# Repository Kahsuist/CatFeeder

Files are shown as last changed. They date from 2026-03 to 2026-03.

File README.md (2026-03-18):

# Автокормушка для кота. ESP-32, WiFi, Bluetooth, расписание.






 - Автоматическая кормушка для домашнего питомца. Не нужно следить за миской кота и контролировать его норму, чтобы он не превратился в колобка, как некоторые домашние питомцы. Экономит время и устраняет одну заботу - помнить о кошачьей миске.

## Возможности

- Не очевидная функция - возможность дрессироваки кота.
- Расписание гибко задается со смартфона через bluetooth.
- Имеет внутренние часы с синхронизацией в интернет, благодаря чему по расписанию выдает корм по норме.
- Имеется педаль экстренной подачи, которую может нажать и сам кот, если научится.
- Так же экстренно можно насыпать корм со смартфона.
- Расписание сохраняется в постоянной памяти и не теряется после отключения питания.
- Емкость контейнера 3 литра в текущем исполнении.
- Имеется защита от застревания корма с попытками протолкнуть.

## Фото устройства

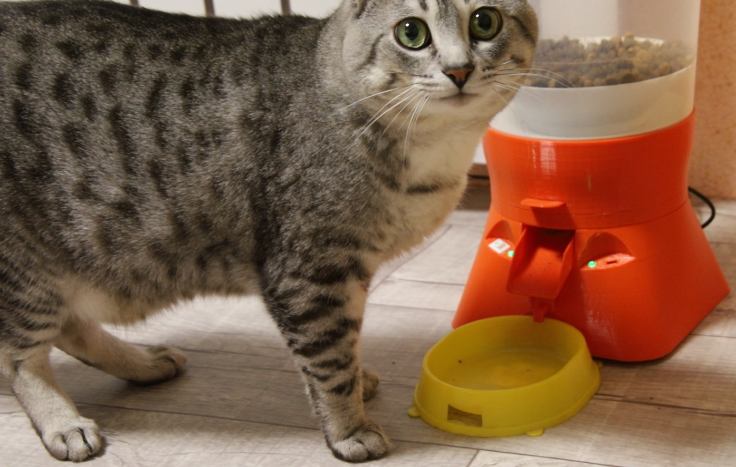
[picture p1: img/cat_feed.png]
Собранное устройство сверху
  
*Собранное устройство. И кот!*

## Электрическая схема

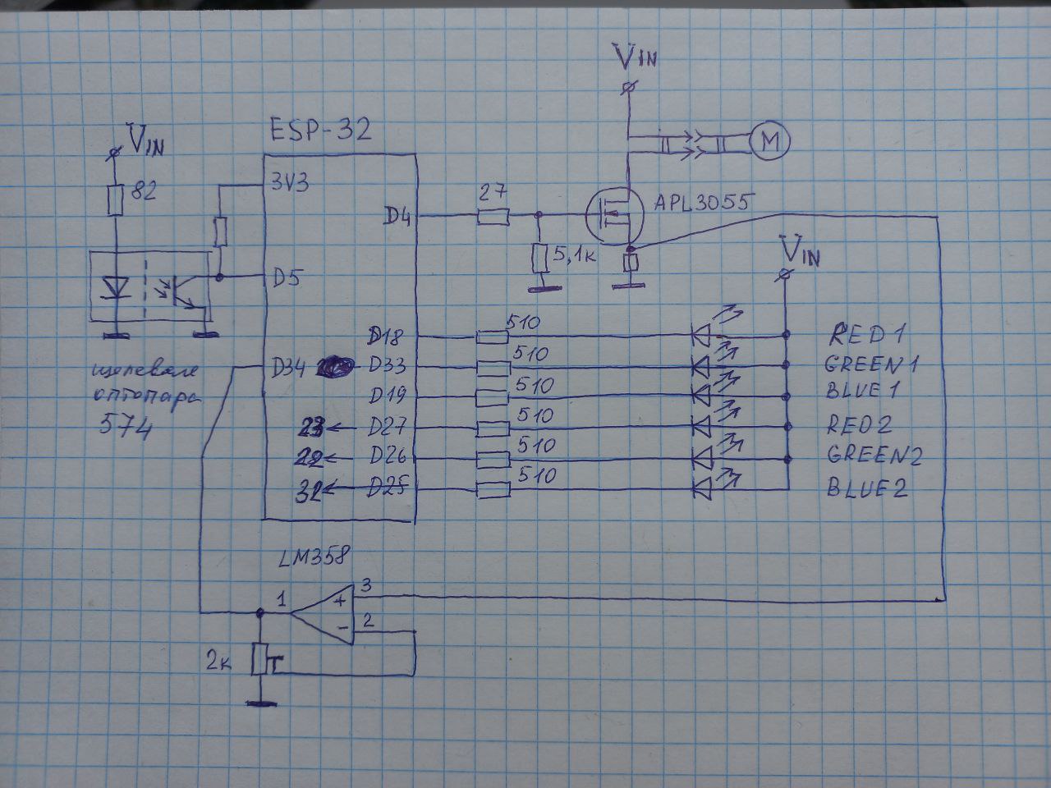
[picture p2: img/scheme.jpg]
Схема на бумаге
  
*Полная электрическая схема*

Подробные файлы схемы:  
- (в планах) ~~[KiCad проект → schematic.kicad_sch](hardware/schematics/)~~
- (в планах) ~~[Экспорт в PDF → schematic.pdf](hardware/schematics/schematic.pdf)~~

## Как открыть и собрать проект

1. Для прошивки микроконтроллера используется Arduino, файл kormushka.ino (файл копируй вместе с папкой, т.к. ардуино требует одноименных названий того и другого). Перед прошивкой внеси данные своей WiFi-сети.
2. Детали кормушки напечатаны на 3д принтере, STL-модели находятся в папке 3Dmodels. ВАЖНО!!! Поскольку это был первый экземпляр, то без мелких ошибок не обошлось, по этому имеются проставки и удлинители. В будущем если проект вызовет интерес, планирую переработать модели, чтобы сборка происходила без лишних телодвижений. В данной версии потребуется не только склейка но и подрезка. Часть деталей изначально задумана из двух половинок, так как напечатать их на принтере целиком крайне не выгодно по филаменту. Проще склеить. Я печатал PETG, он не воняет и легко склеивается дихлорметаном.
3. Радиоэлектроныне компоненты: ESP32, двигатель с редуктором с алиэкспресс JGA25-370 с 16-25 об/мин. 6-12 вольт. Важно, чтобы двигатель давал достаточный момент при напряжении в 5 вольт. Я использовал двигатель с редуктором привода колес от робота-пылесоса на 12 вольт - он такой же, как на али.
4. Полевой ключ APL3055 - любой подобный выдержит ток до 1-2 ампер.
5. Щелевая оптопара тоже дешевая и широкоприменяемая. Я использовал из того-же робота-пылесоса, на ней обозначение 574. Но встречал такие же в принтерах, ксероксах, сканерах и прочих приборах с конечными датчиками-оптопарами.
6. Операционник LM358 так же очень широко распространен.
7. Светодиоды RGB в одном корпусе с общим анодом. На алиэкспресс 50 штук за 120 руб.
8. Резисторы любые. Я паял как прототип на макетке, мне были удобны smd.

## Как использовать

1. Насыпал корм, включил в розетку. Устройство само подключится к WiFi и синхронизирует часы по интернет.
2. В смартфоне открываешь bluetooth-устройства, находишь CatFeeder, подключаешся.
3. Запускаешь любой bluetooth-терминал, коннектишся к выбранному catfeeder-y
4. Список команд<br>
    **SET 7:15 2** - установить, время в часах:минутах, количество доз. Одна доза = один сектор поворота (из шести). 2 - соответственно два сектора. В моем случае 1 доза это 15 грамм корма. Если поставить 2 то насыплется 30 грамм и так далее.<br>
    **DEL 7:15** - удалить конкретную запись, если она есть.<br>
    **LIST** - показать всё расписание<br>
    **CLEAR** - удалить всё расписание<br>
    **SAVE** - сохранить расписание в память. ВАЖНО!!! Если не сохранить расписание, то оно пропадет после выключения питания.<br>
    **RUN** - насыпать одну дозу корма (15гр.)<br>

## Зависимости / Требования

Для прошивки под линукс открываем терминал, вводим команду *sudo chmod a+rw /dev/ttyACM0* либо *sudo chmod a+rw /dev/ttyUSB0*, чтобы система получила доступ к устройству, то есть задать права доступа. Теперь можно прошивать из ардуино. Как это делается в Windows - расскажите, добавлю сюда. Предполагаю, что понадобится установка драйверов и другие танцы с бубном.

## Disclaimer

Это первая версия readme, в ней обязательно должны быть ошибки и недочеты, по этому обращайтесь по контактам ниже, с вашей помощью устраним баги для будущих посетителей. 

Это рабочий отлаженный прототип. Но пердполагается апгрейд проекта (аккумуляторы, приложение на смартфон, печатная плата с герберами под производство и др.)
Используй на свой страх и риск.  

Сообщения об ошибках / PR приветствуются!

## Лицензия

MIT License — см. файл [LICENSE](LICENSE)

## Контакты

Если хотите со мной связаться: телега *@kahsuist*

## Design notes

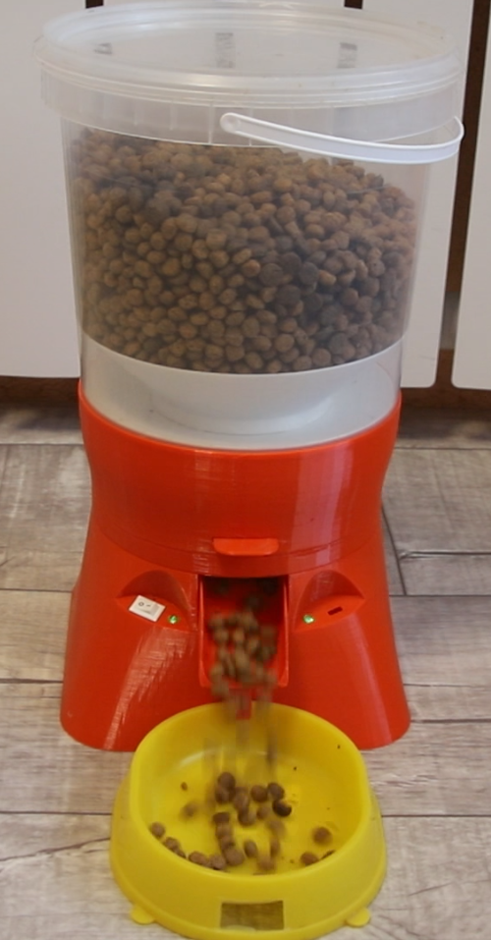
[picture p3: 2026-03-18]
img/catfeeder.png

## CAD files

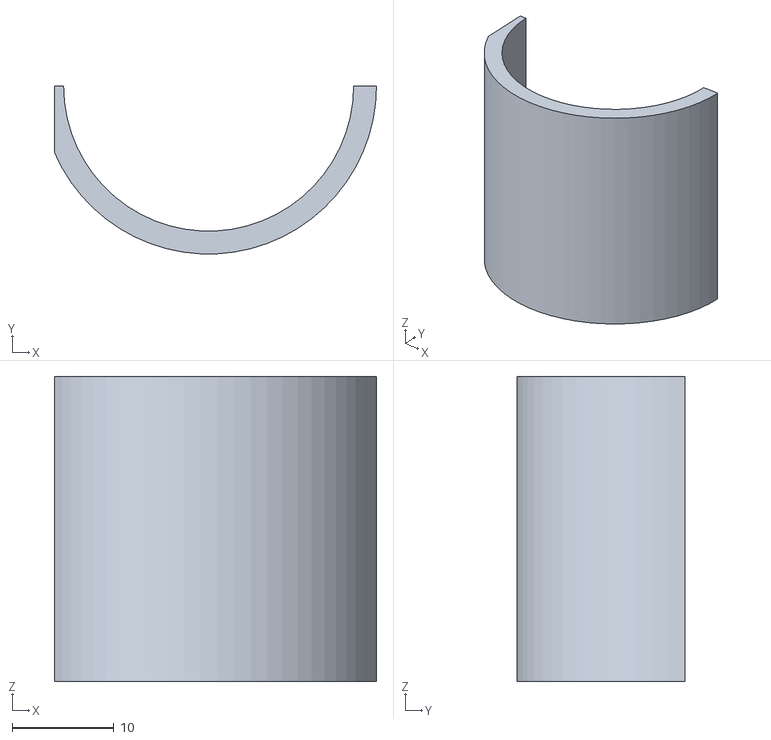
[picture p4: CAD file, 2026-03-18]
3Dmodels/накладка.STL
31.6 x 16.5 x 30.0

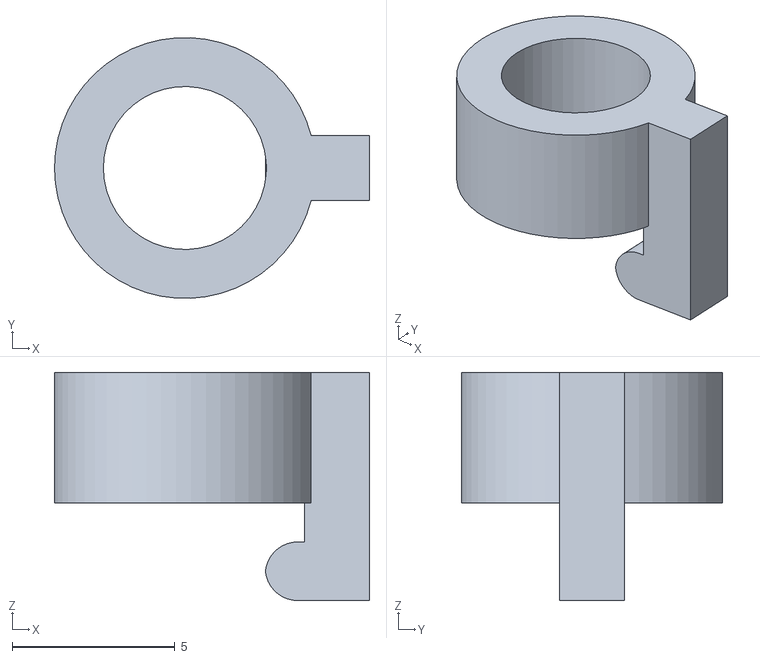
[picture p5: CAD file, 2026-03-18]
3Dmodels/LEDpoint.STL
9.66 x 7.99 x 7.00

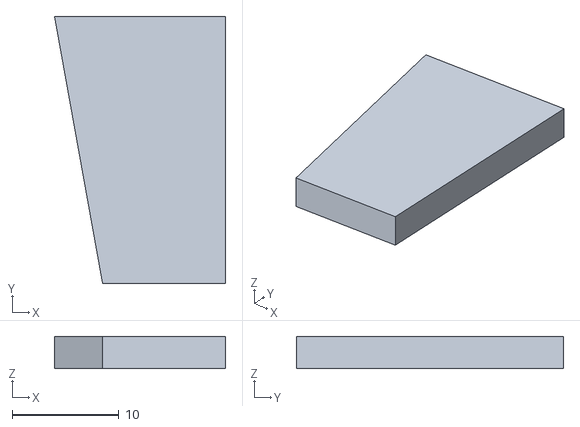
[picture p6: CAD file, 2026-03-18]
3Dmodels/ребро.STL
16.0 x 25.0 x 3.00

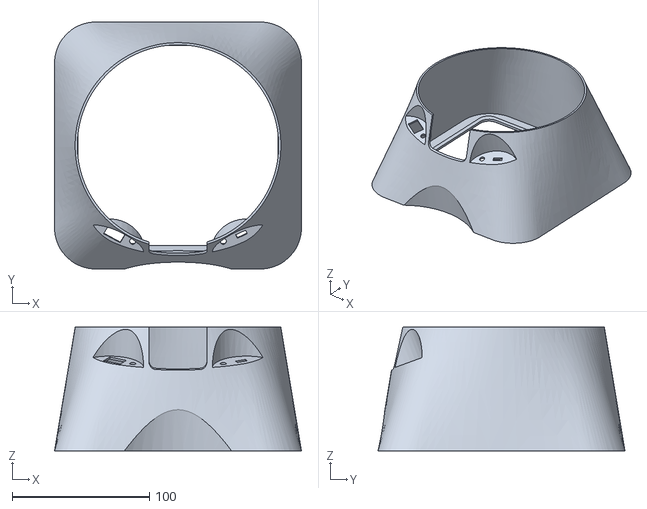
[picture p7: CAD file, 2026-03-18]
3Dmodels/основ_корпус.STL
180.0 x 180.0 x 90.0

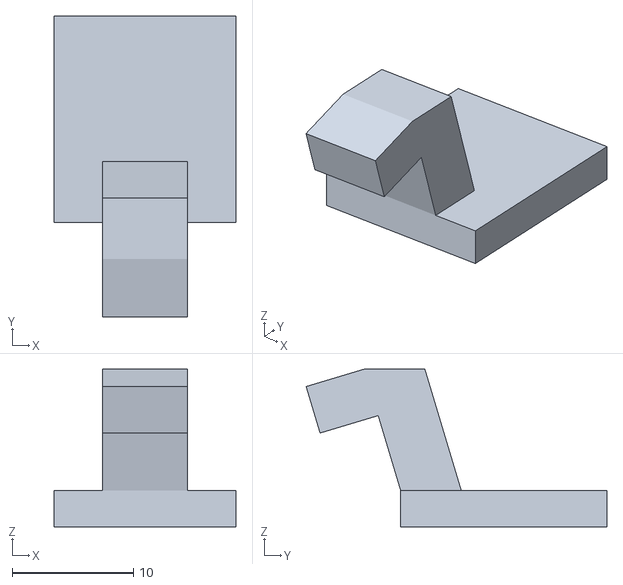
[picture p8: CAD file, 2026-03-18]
3Dmodels/крюк.STL
15.0 x 24.8 x 13.0

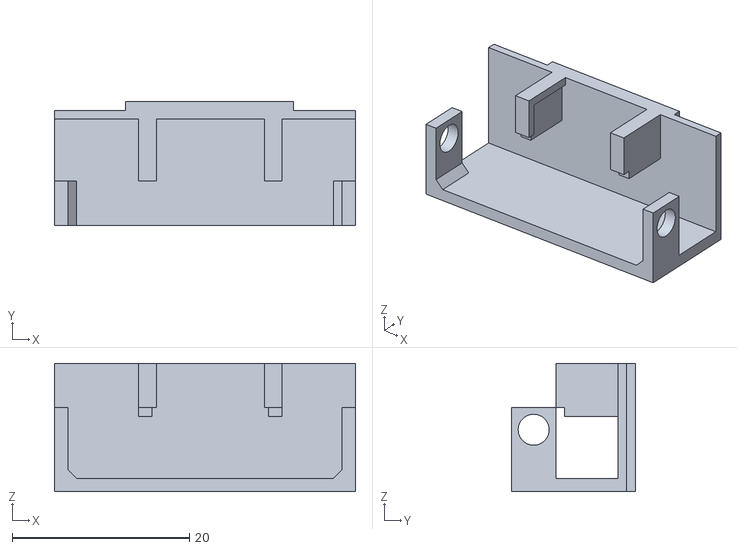
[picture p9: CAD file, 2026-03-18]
3Dmodels/опора_педали.STL
34.0 x 14.0 x 14.5

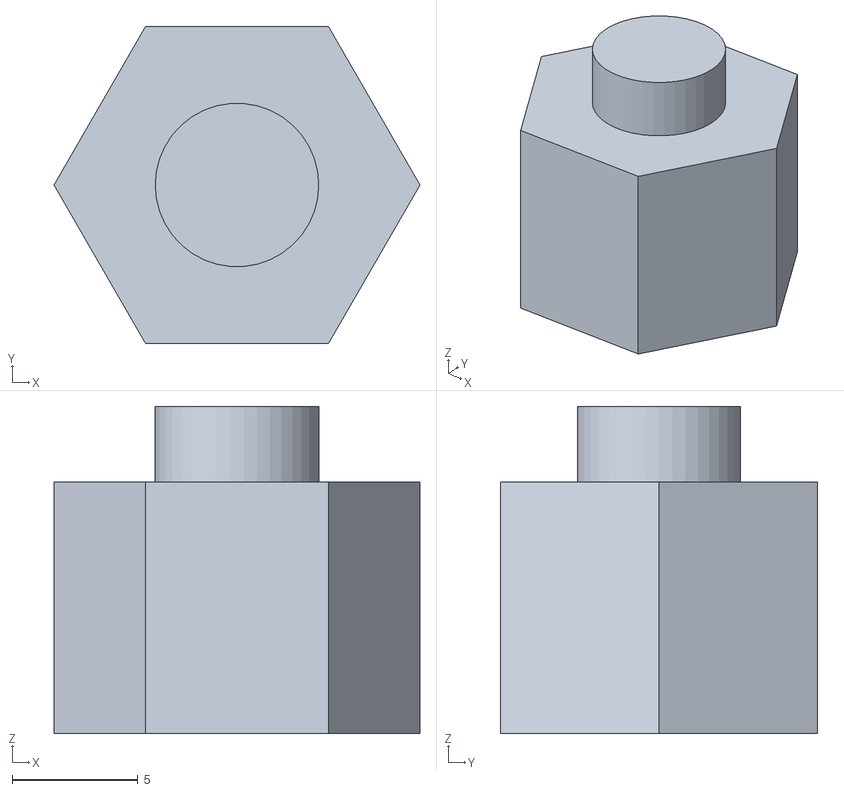
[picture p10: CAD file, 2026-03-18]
3Dmodels/шегранаст.STL
14.5 x 12.6 x 13.0

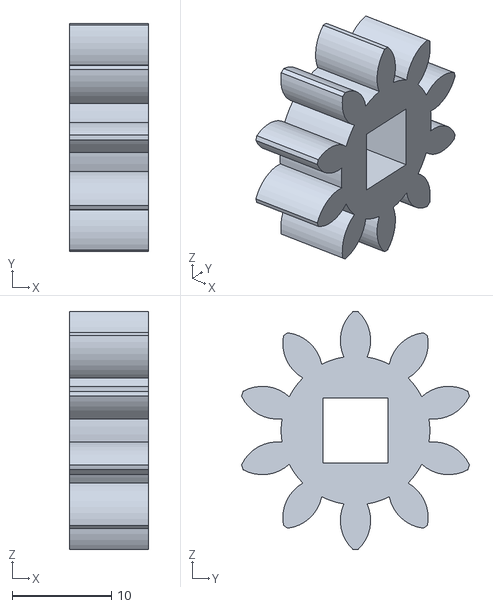
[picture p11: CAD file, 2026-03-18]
3Dmodels/10зубьев.STL
8.00 x 23.0 x 24.0

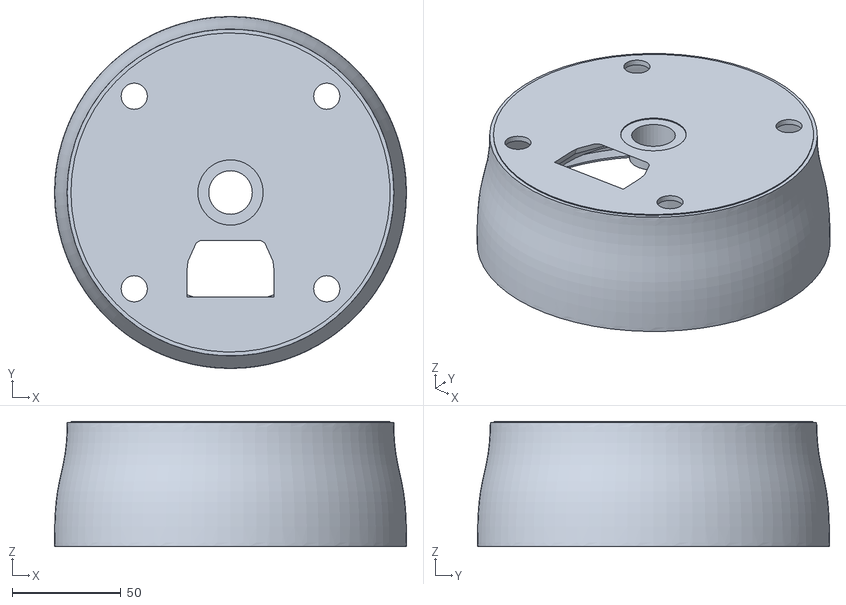
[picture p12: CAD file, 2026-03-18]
3Dmodels/лотокА.STL
161.6 x 161.6 x 57.5

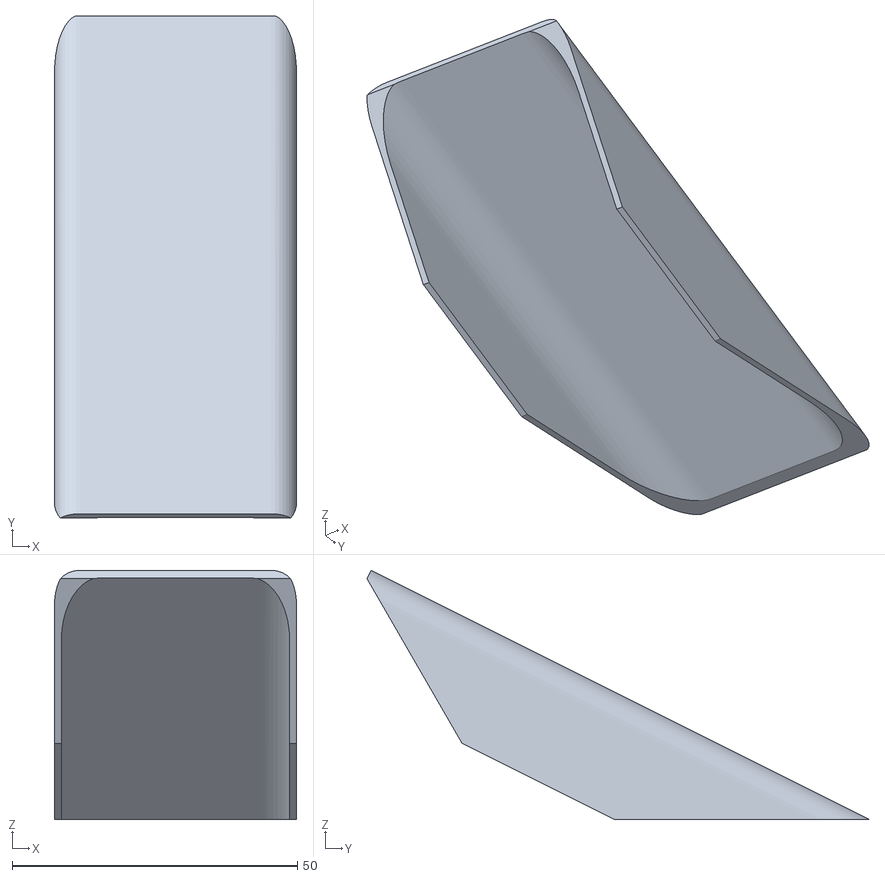
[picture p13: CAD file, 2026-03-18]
3Dmodels/лотокБ.STL
42.4 x 87.9 x 43.7

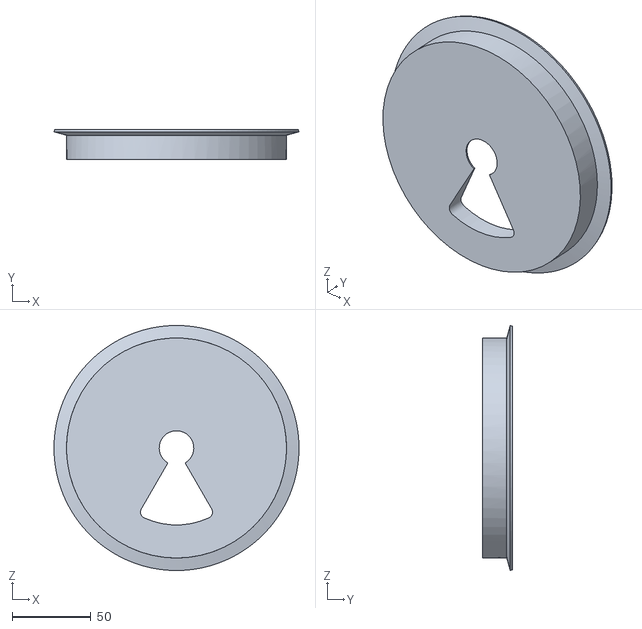
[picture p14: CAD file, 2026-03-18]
3Dmodels/конус_дноА.STL
155.9 x 19.0 x 156.0

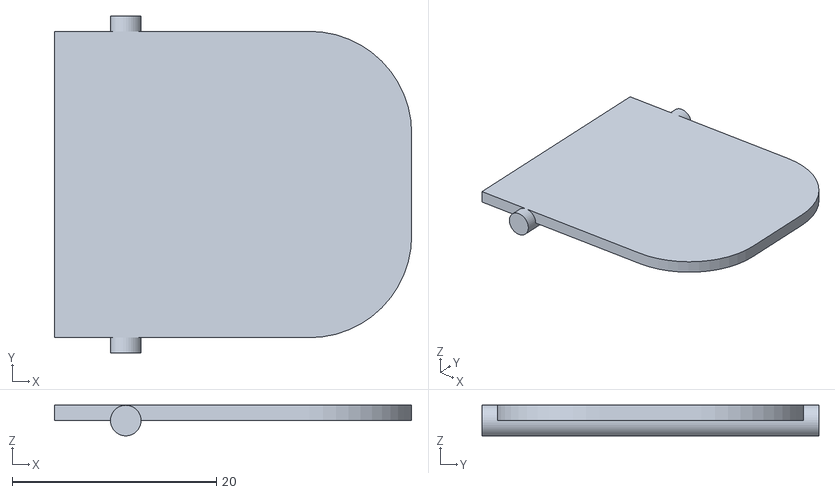
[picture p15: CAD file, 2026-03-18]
3Dmodels/педаль.STL
35.0 x 33.0 x 2.99

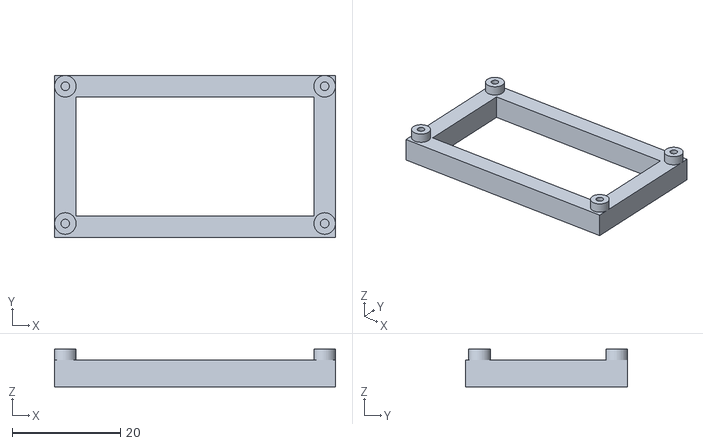
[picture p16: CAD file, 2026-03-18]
3Dmodels/подложка.STL
52.0 x 30.0 x 7.00

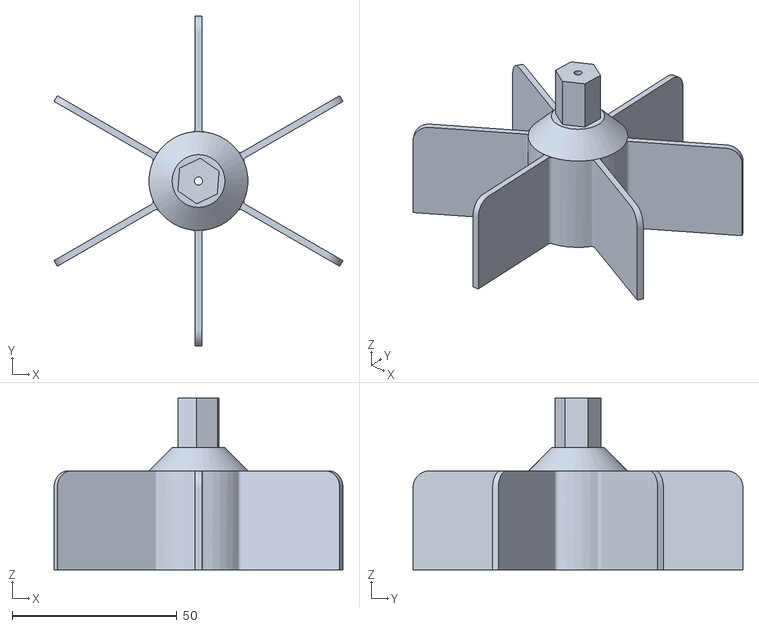
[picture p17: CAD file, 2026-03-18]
3Dmodels/звезда.STL
87.6 x 100.0 x 52.0

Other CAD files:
3Dmodels/мотун.STL
3Dmodels/30зубьев.STL
3Dmodels/конус.STL
3Dmodels/основание.STL
3Dmodels/конус_дноБ.STL
3Dmodels/конус_наддно.STL
3Dmodels/проставка.STL
3Dmodels/шестигранник.STL

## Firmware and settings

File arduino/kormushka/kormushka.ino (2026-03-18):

#include <WiFi.h>
#include <NTPClient.h>
#include <TimeLib.h>
#include <Wire.h>
#include <BluetoothSerial.h>
#include <Preferences.h>
#include <Arduino.h>

// sudo chmod a+rw /dev/ttyUSB0
// sudo chmod a+rw /dev/ttyACM0

#define R1 GPIO_NUM_18
#define G1 GPIO_NUM_33
#define B1 GPIO_NUM_19
#define R2 GPIO_NUM_23    //23
#define G2 GPIO_NUM_22    //22
#define B2 GPIO_NUM_32    //32
#define BTN GPIO_NUM_15
#define datchik GPIO_NUM_5
#define motor GPIO_NUM_4

#define termod GPIO_NUM_34

#define POROG     1

BluetoothSerial SerialBT;
Preferences prefs;

struct FeedingTime {
  int hour;
  int minute;
  int portions;
};

const int MAX_SCHEDULE = 10;   // можно задать до 10 событий
FeedingTime schedule[MAX_SCHEDULE];
int scheduleCount = 0;

// Замените на свои данные Wi-Fi
const char* ssid = "*****";
const char* password = "#####";

// Укажите временной сервер и часовой пояс
const char* ntpServer = "pool.ntp.org";
const long utcOffsetInSeconds = 10800; // 10800 -> GMT+3
unsigned long lastRunCounter1m = 0;
int run = 0;

WiFiUDP udp;
NTPClient timeClient(udp, ntpServer, utcOffsetInSeconds);

int blink = 0;

/* этапы:
- тест заряда
+ два светодиода - 6 контактов
+ мотор
+ оптический датчик
+ получение команд с блютус
- приложение на смартфон
- сервер вайфай для настроек
*/

void allLedsOff()
{
    //Serial.println("allOff");
    digitalWrite(R1, 0x1);
    digitalWrite(G1, 0x1);
    digitalWrite(B1, 0x1);
    digitalWrite(R2, 0x1);
    digitalWrite(G2, 0x1);
    digitalWrite(B2, 0x1);
    digitalWrite(motor, 0x0);
}

void blue() {
  digitalWrite(B1, 0x0);
  digitalWrite(B2, 0x0);
  delay(1);
  digitalWrite(B1, 0x1);
  digitalWrite(B2, 0x1);
}

void red() {
  digitalWrite(R1, 0x0);
  digitalWrite(R2, 0x0);
  delay(1);
  digitalWrite(R1, 0x1);
  digitalWrite(R2, 0x1);
}

void green() {
  digitalWrite(G1, 0x0);
  digitalWrite(G2, 0x0);
  delay(1);
  digitalWrite(G1, 0x1);
  digitalWrite(G2, 0x1);
}

void leds() {
  //blue();
  //red();
  green();
}

void connectingIndicate() {
  if(blink % 2 == 0) {
    digitalWrite(R1, 0x0);
    digitalWrite(G1, 0x0);
    digitalWrite(B1, 0x0);
    digitalWrite(R2, 0x0);
    digitalWrite(G2, 0x0);
    digitalWrite(B2, 0x0);
  }
  else {
    digitalWrite(R1, 0x1);
    digitalWrite(G1, 0x1);
    digitalWrite(B1, 0x1);
    digitalWrite(R2, 0x1);
    digitalWrite(G2, 0x1);
    digitalWrite(B2, 0x1);
  }
  blink += 1;
}

bool datchikChanged() {
  static int prevD = 1;
  if(prevD==1 && digitalRead(datchik)==0) {
    prevD = digitalRead(datchik);
    return true;
  }
  prevD = digitalRead(datchik);
  return false;
}

void setup() {
  pinMode(R1, OUTPUT);
  pinMode(G1, OUTPUT);
  pinMode(B1, OUTPUT);
  pinMode(R2, OUTPUT);
  pinMode(G2, OUTPUT);
  pinMode(B2, OUTPUT);
  //pinMode(BTN, INPUT);
  pinMode(datchik, INPUT);
  pinMode(motor, OUTPUT);
  pinMode(termod, INPUT);
  allLedsOff();
  pinMode(BTN, INPUT_PULLUP);
  //pinMode(datchik, INPUT_PULLUP);

  Serial0.begin(115200);
  SerialBT.begin("CatFeeder");

  // загрузка расписания
  prefs.begin("catfeed", true);
  scheduleCount = prefs.getInt("count", 0);
  if (scheduleCount > 0 && scheduleCount <= MAX_SCHEDULE) {
    prefs.getBytes("sched", schedule, sizeof(FeedingTime) * scheduleCount);
  }
  prefs.end();

  // Подключение к Wi-Fi
  WiFi.begin(ssid, password);

  while (WiFi.status() != WL_CONNECTED) {
    delay(500);
    Serial0.println("Подключение к Wi-Fi...");
    connectingIndicate();
  }
  Serial0.println("Подключено к Wi-Fi");
  allLedsOff();

  // Инициализация NTP клиента
  timeClient.begin();

  Serial.println("Bluetooth CatFeeder ready");
}

bool checkStuck() {
  static int value = 0;
  int raw_current = analogRead(termod);

  float current = raw_current * 3.3 / 4095.0 * 1;
  Serial.print("Motor current = ");
  Serial.print(current);

  if (current > POROG) value++;
  else value = 0;

  Serial.print("; threshold ");
  Serial.println(value);

  if (value > 10) { value = 0; return true; }
  else return false;
}

void avaria() {
  run = 0;
  digitalWrite(motor, 0x0);

  for (int i = 0; i<20; i++) {
    for (int j = 0; j<100; j++) {
      red();
      delay(5);
    }
    delay(500);
  }
  run = 1;
  digitalWrite(motor, 0x1);
}

void loop() {
  
  
  static unsigned long lastUpdate = 0; // Переменная для хранения времени последнего обновления

  static unsigned long timeToUpdate = 10000;
  //if(counter<40) { counter += 1; } else timeToUpdate = 120000;

  // Обновляем время из NTP раз в минуту
  if (millis() - lastUpdate > timeToUpdate) { // Каждые 60 секунд
    timeClient.update();

    // Получаем текущее время из NTP
    unsigned long epochTime = timeClient.getEpochTime();

    // Устанавливаем локальное время
    setTime(epochTime); // Учитываем смещение по времени  + utcOffsetInSeconds
    lastUpdate = millis(); // Обновляем время последнего обновления
  }

  // Получаем текущее локальное время
  int hours = hour();
  int minutes = minute();

  // Форматируем время в строку "HH:MM"
  String formattedTime = String(hours) + ":" + (minutes < 10 ? "0" : "") + String(minutes);

  //***********************************************

  // приём команд Bluetooth
  if (SerialBT.available()) {
    String cmd = SerialBT.readStringUntil('\n');
    cmd.trim();

    if (cmd.startsWith("SET")) {
      int h, m, p;
      sscanf(cmd.c_str(), "SET %d:%d %d", &h, &m, &p);
      if (scheduleCount < MAX_SCHEDULE) {
        schedule[scheduleCount++] = {h, m, p};
        SerialBT.println("OK");
      } else {
        SerialBT.println("ERR FULL");
      }
    }

    else if (cmd.startsWith("DEL")) {
      int h, m;
      sscanf(cmd.c_str(), "DEL %d:%d", &h, &m);
      for (int i = 0; i < scheduleCount; i++) {
        if (schedule[i].hour == h && schedule[i].minute == m) {
          for (int j = i; j < scheduleCount - 1; j++) schedule[j] = schedule[j + 1];
          scheduleCount--;
          SerialBT.println("DELETED");
          break;
        }
      }
    }

    else if (cmd == "LIST") {
      for (int i = 0; i < scheduleCount; i++) {
        SerialBT.printf("%02d:%02d -> %d\n", schedule[i].hour, schedule[i].minute, schedule[i].portions);
      }
      if (scheduleCount == 0) SerialBT.println("EMPTY");
    }

    else if (cmd == "CLEAR") {
      scheduleCount = 0;
      SerialBT.println("CLEARED");
    }

    else if (cmd == "SAVE") {
      prefs.begin("catfeed", false);
      prefs.putInt("count", scheduleCount);
      prefs.putBytes("sched", schedule, sizeof(FeedingTime) * scheduleCount);
      prefs.end();
      SerialBT.println("SAVED");
    }

    else if (cmd == "RUN") {
      run = 1;
      SerialBT.println("RUN");
    }
  }

  //***********************************************


  // раз в минуту
  if (millis() - lastRunCounter1m >= 60000) {
    lastRunCounter1m = millis();
    // Выводим время в Serial Monitor
    Serial0.println(formattedTime);
    //if(minutes%5==0) run = 2;

    //***********************************************
    for (int i = 0; i < scheduleCount; i++) {
      // для отладки наглядность: печать расписания в консоль
      Serial.printf("%02d:%02d -> %d\n", schedule[i].hour, schedule[i].minute, schedule[i].portions);
      if (hours == schedule[i].hour && minutes == schedule[i].minute) {
        run = schedule[i].portions;
      }
    }
    //***********************************************

  }

  if(digitalRead(BTN)==0) {
    Serial0.println("button pressed");
    run = 1;
  }

  if(run) {
    digitalWrite(motor, 0x1);
    Serial.print("datchik = ");
    Serial.print(digitalRead(datchik));
    Serial.print(";  run = ");
    Serial.println(run);
    if (checkStuck()) avaria();
  }
  else digitalWrite(motor, 0x0);

  if(datchikChanged()) {
    run -= 1;
    Serial.print("run - 1;  run = ");
    Serial.println(run);
    if(run<0) run = 0;
  }

  leds();
  
  delay(20);
}

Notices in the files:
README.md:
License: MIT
